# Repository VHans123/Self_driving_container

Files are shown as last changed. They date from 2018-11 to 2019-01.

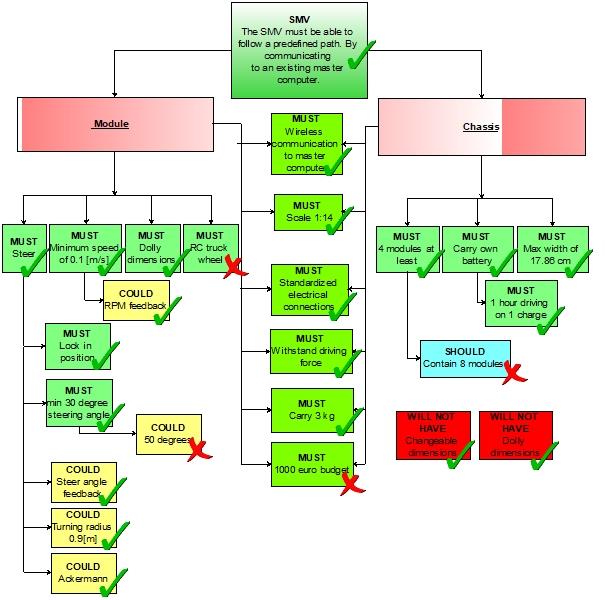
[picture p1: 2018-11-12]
Dallas/docs/Pictures/Check list requirements.jpg

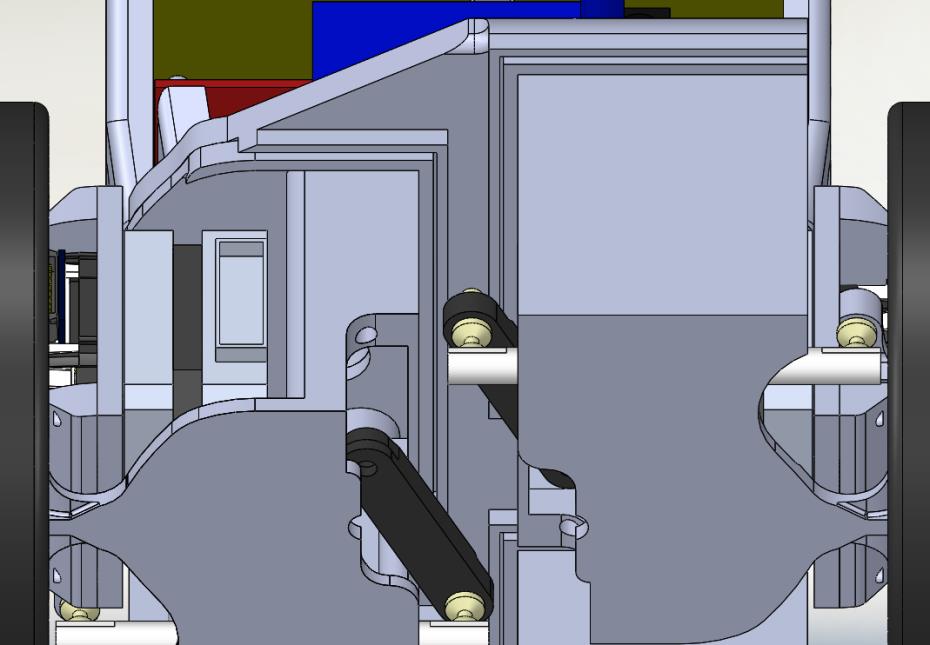
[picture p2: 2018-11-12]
Dallas/docs/Pictures/Chassis improvements 2.jpg

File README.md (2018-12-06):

# Self driving container

This is the repository of the self driving container chassis called Dolly.

It is split up in three main parts.

1 The first one is called Drawings. In this part you can find all the SolidWorks drawings of the chassis.

2 The second one is called Electronics. In this part you can find the Schematic design and PCB design of the PCB. These files are made in Multisim and Ultiboard.

3 The third one is called Software. In this part you can find all the Matlab and Simulink files. These files are used to receive data from the XBee. Also these files contain the software for controlling the wheel speed and angle.

The steering angle and speed of the Dolly is given by the Jetson. This Jetson uses a vision system. Because the vision system and the Dolly are two different parts, each one has it's one GitHub repositoy. Below you can find a link to the repository of the Jetson.

https://github.com/jostyijzer/ArUco-Detection

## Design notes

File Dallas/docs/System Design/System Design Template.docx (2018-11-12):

# System Design Template

Smart Quarter Vehicle

Status: Draft

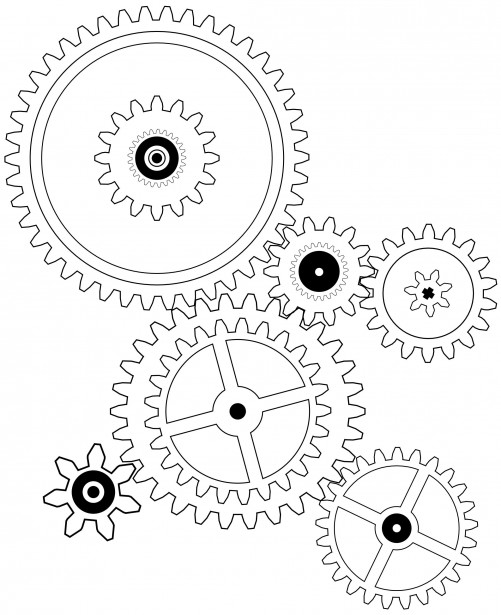
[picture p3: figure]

Name | Student nr
William Marcelissen | 507428
Chris van der Spek | 561633
Gerran Jansma | 521675
Teun van den Burg | 530770

# 1 Intro

During the project a Smart Modular Vehicle (SMV) will be designed, developed and built.

The Smart Modular Vehicle consists of a chassis and multiple identical and interchangeable steering and driving modules. The chassis and wheel dimensions will be scaled 1:14 with respect to a real truck. This SMV will be able to follow a predefined path by communicating with a master computer which has an overview of the predefined path via a camera hanging or hoovering above the path.

The SMV will be designed, developed and built for HAN Automotive Research. The SMV will provide them a modular platform which can simulate multiple truck chassis outlay. HAN AR can use this SMV for future and ongoing projects like the “Drone assisted truck navigation project”.

This system design document will first provide a general overview of the system and the goals of the project. It also contains a more detailed architecture and design of the system and all of its subsystems. These, more detailed, designs will both discuss hardware and software. The document will conclude with the design and architecture of the interface which will allow communication between the different subsystems. In this document the system will be visualised in diagrams to give the reader a better understanding of how all subsystems are connected.

# 2 General Overview and Design

## 2.1 General Overview

The system exists of the platform and at least four modules. The microcontroller of the system is placed on the platform and controls the steering, accelerating and braking of the four modules. The microcontroller communicates with the master computer which sends a signal that contains the predefined path.

## 2.2 System Context

Figure 1 Contextual Diagram

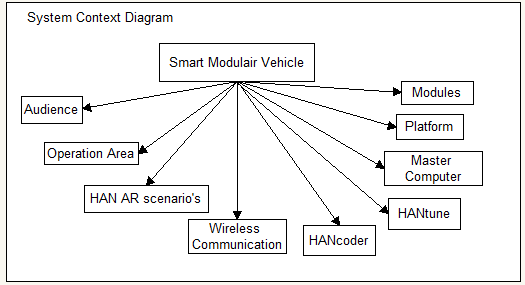
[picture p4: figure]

## 2.3 Use Cases

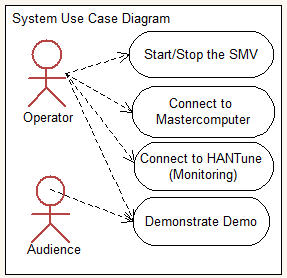
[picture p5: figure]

Figure 2 Use Case Diagram

### 2.3.1 System Components

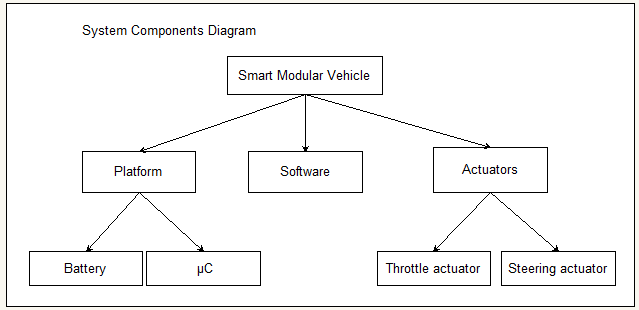
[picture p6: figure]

Figure 3 Component Diagram

## 2.4 Assumptions

- For creating and sending the predefined path to the SMV, the existing software developed by previous students will be used.
- The main software used for programming and debugging will be Matlab, Simulink, HANCoder and HANTune
- The end user can expect a Smart Modular Vehicle that is capable of driving the predefined path.
- The Smart modular Vehicle exist at least out of 4 modules (2 driving and 2 steering) but a different setup with more modules is possible.

## 2.5 Constraints

- The algorithms of the previous project group has to be investigated before changing and implanting is possible.
- Before the algorithms can be implemented, the platform with 4 modulus must be in prototype phase.
- Because the SMV is a prototype and there is a limited time frame, the end-user environment is not a high priority.

## 2.6 Risks

Because the project takes only roughly 3 months. The main focus will be the electrical and programming part of the system. Therefor the design of the SMV will be simple but sturdy, so no fancy boltless plug and play system for the modules will be developed. In this way there is more time that will be spent on programming and improving the system. What is more in the scope of this project.

# 3 Design Considerations

## 3.1 Problem Statement

The current vehicles are limited in their specifications and dimensions. Fixed truck setups and imprecise steering & driving makes these RC trucks undesired to work with.

As stated above, the current RC trucks are not precise enough in steering and driving. This concludes in a lot of steering actions that can be avoided with a better system. Also is HAN-AR limited in setup options, because of the fact that the truck setups are depending on the purchased vehicles.

## 3.2 Goals

The goal is to create a platform which makes use of wheel modules. This platform must drive a path that is predefined by the master computer.

- Within this main goal, a sub-goal is to create modular wheel units which receives input from the master PC.
- Another goal is to create a chassis that can accommodate at least 4 modules. The chassis needs standardised connections to connect with the modules.
- Also the modules will include (HANcoder) software to work properly.

# 4 System Architecture and Design

This chapter describes the different system aspects that could be used for the SMV. First thing that will be described is a logic view of the different system aspects that are going to be used on the SMV. The hardware architecture of the SMV will be described in different diagrams, after the logic view. The next step is also about architecture but then about the software that needs to be made. The last subject in this chapter is the internal communication of the SMV. All of this will be shown in diagrams and an explanation of the diagrams will be given.

## 4.1 Logical View

A logic view of a product is what it can do after it is turned on and off. The logical view of the SMV is presented here below.

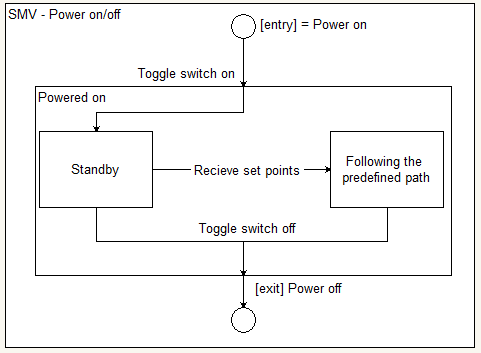
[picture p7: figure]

Figure 4 Logical view

## 4.2 Hardware Architecture

The hardware Architecture will be divide by the chassis and the module. The diagrams of the hardware architecture are shown below.

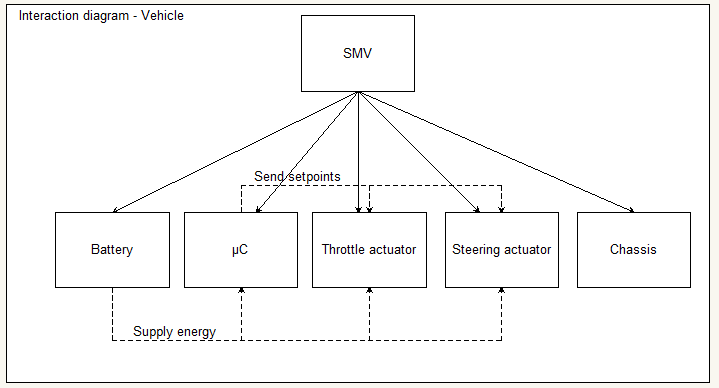
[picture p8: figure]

Figure 5 Interaction diagram of the vehicle

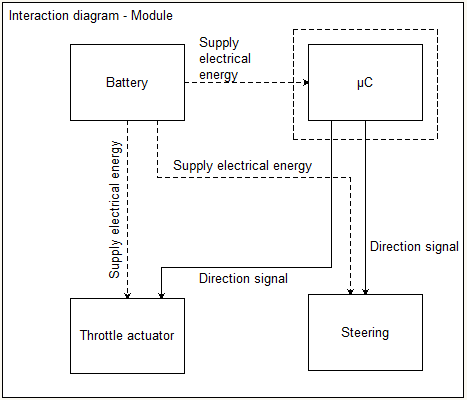
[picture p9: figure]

Figure 6 Interaction diagram of the module

## 4.3 Software Architecture

There needs to be a wireless connection between the master computer and the microcontroller. The microcontroller receives steering and throttle setpoints from the master computer. These setpoints have to be converted to a signal for the throttle and steering actuators of each individual module. Converting a single steering setpoint to multiple independent steering angles according to Ackermann is also done by the microcontroller.

## 4.4 Internal communication Architecture

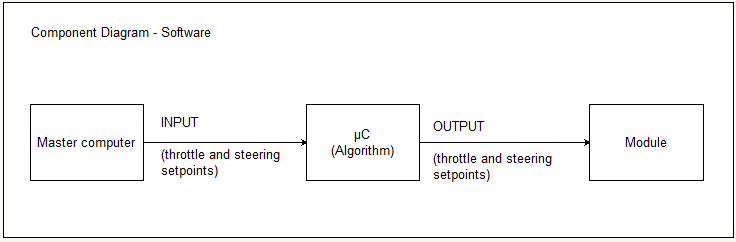
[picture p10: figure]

The communication of the SMV will be wireless from master computer to mainboard. The diagram of the wireless communication is shown in figure 7.

Figure 7 Wireless Interaction Diagram

# 5 System Detailed Design

## 5.1 Hardware Detailed Design

The SMV will contain both purchased components as components designed and built by the project group. To have a good overview of the hardware designed some components will be elaborated more detailed.

### 5.1.1 Chassis

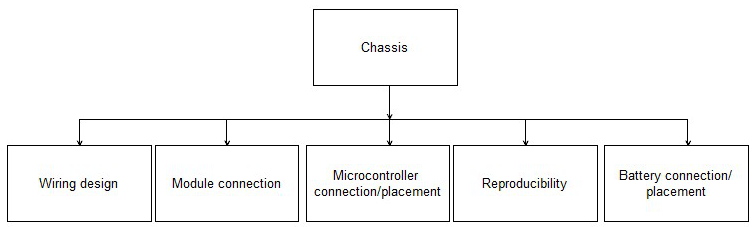
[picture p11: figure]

Figure 8 Chassis functions

The chassis is a large hardware component of the system. This component will carry all other subsystems, therefore it is important to have a more detailed look at the chassis.

Module connection

In the set of requirements is stated that de chassis must be able to carry at least four modules. These modules must be interchangeable. Therefore the connection between chassis and module must be modular. Another requirement states that the connection must be able to withstand the driving forces caused by driving the predefined path.

Mainboard connection/placement

The mainboard will be controlling all the modules and receive and process the signals coming from the master computer. The placement of this mainboard will be crucial for the design of the wiring.

Reproducibility

Because HAN AR is planning on using the SMV in different future projects, it is important for them to make more SMV’s. Therefore the design of the chassis should be accessible and adjustable to simulate a different vehicle. Also the production of the chassis should be easy to repeat.

Battery connection/placement

Being a heavy component the placement and connection of the battery is important for the design of the chassis.

### 5.1.2 Module

The modules are the most complex hardware components to be designed and built. A lot of functionalities of the SMV are dependent on the module design and development. Because of its importance the module design will be further specified.

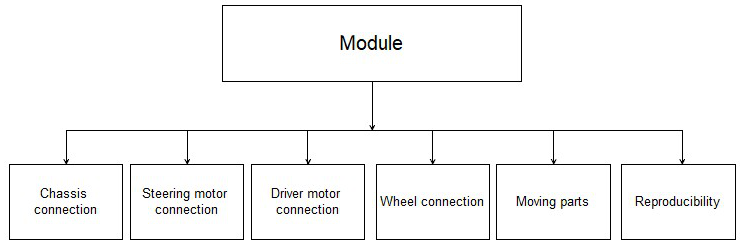
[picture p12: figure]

Chassis connection
This connection must be able to withstand the driving forces while driving the predefined path. See 5.1.1 Module connection.

Figure 9 Module functions

Steering motor connection

The steering motor will be connected to the module and the rest of the drivetrain. The connection to the module has to be rigid to set and hold a precise steering angle.

Driver motor connection

The driver motor needs a rigid connection to be able to deliver the driving force.

Wheel connection

HAN AR requires the use of existing 1:14 RC truck wheels.

Moving parts

Because of the steering capability of the modules there will be moving parts inside the module. This puts extra pressure on the tolerances of the hardware. While designing the modules this is an important fact to keep in mind.

Reproducibility

The module must be easy to reproduce to extend the SMV in future projects. This means accessible design and easy production methods.

## 5.2 Software Detailed Design

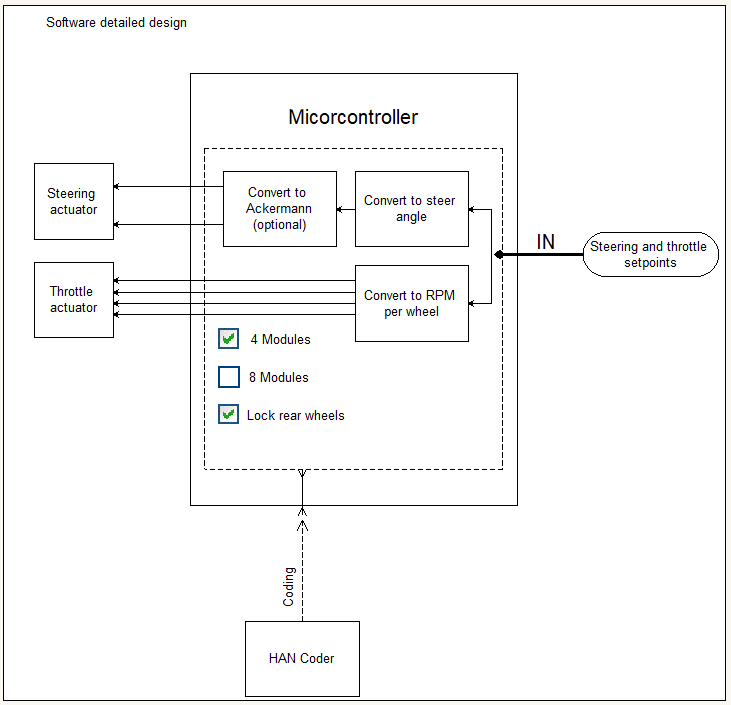
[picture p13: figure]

Figure 10 Software detailed design

The SMV will be communicating with the existing master computer, this computer will send out a signal to the SMV containing PWM values. The software programmed in de microcontroller will translate this to driving and steering the vehicle.

HAN Coder

The programming will be programmed using the model based HAN Coder software. Simulink blocks represent different functionalities. By placing these blocks a logical block diagram can be created. The C code will automatically be created by HAN Coder and can be flashed to the microcontroller.

Converting signals

The mainboard will receive its input from the master computer. The microcontroller has to convert this signal into an actual driving signal to the driver and steering motors. The driving signal the microcontroller has to transmit depends on the type of motors that will be used. The SMV might also get Ackermann steering behaviour, this will result in extra calculations of the microcontroller and different steering angles for each wheel.

Set up

HAN AR wants to use the SMV with a varying amount of modules connected. With the 4 wheel setup it should also be possible to lock the rear wheel which will prevent them from steering. This way a two wheel steering truck can be simulated. When changing the set up the driving signal also has to change. Therefore it is important that the set up changes in the software are straightforward and easy to make.

# 6 External Interfaces

Looking at the external interfaces used within this project, the main external interface is the Master computer. This project works with a predefined path that the Master computer sends in PWM signals to the SMV. The path can be defined in the master computer, or the path can be defined by the drone. Either way the master computer has coordinates of the path and sends it to the SMV.

## 6.1 Interface Architecture

Referring to the SCD, the master computer is a part of the whole system. The Master computer sends the PWM signals to the chassis. The Master computer receives the X, Y and angle of the vehicle via the drone. The logarithm calculates the PWM values to get the desired position of the vehicle.

Figure 11 System Context Diagram

## 6.2 Interface Detailed Design

Looking at the external interfaces, the master computer is the only and most important external interface.

Figure 12 Interaction diagram

Data Direction (Systems viewpoint) | What is interacted? | Details
Send | XCP messages over Zigbee | 4 bytes: Start byte, Steering byte with PWM value, throttle byte with PWM value, stop byte

It is possible that the Drone can send the predefined path to the master computer, in that case the Master computer receives the following data:

Data Direction (Systems viewpoint) | What is interacted? | Details
receive | XCP messages over Zigbee | 4 bytes: Start byte, Byte Marker 1 (X, Y, angle marker), Byte Marker 2(X, Y, angle marker), stop byte

# Appendix A – References

Diagrams:

Pictures:

# Appendix B – Diagram Conventions

These relations are a suggestion on how to use the diagrams. Feel free to add new features to your diagrams. However, if new features need to be added, please look at existing conventions in order to avoid confusion. At HAN-AR some knowledge and experience is present regarding formal modelling languages.

Component Diagram:

| Component (Also used in Interaction Diagrams)
| Component / Subcomponent relation (Also called: Parent/Child, or Super/Sub component)

Interaction Diagram:

| Component (from component diagram)
| Item flow (Anything that flows, e.g. Data, Energy, Fluid, Air)

State Machine Diagram:

| Entry point
| State
| Exit point
| State transition
| Guard, entry or exit criterium

Use Case Diagram:

| (Usually) Human interacting entity. Interaction may be both ways. Usually entails e.g. Operator, End-User, Maintenance staff, Audience, etc.
| A use case. Could also have descendants in order to group use cases.
| Interaction relation
| Descending relation

Document type System Design Template, Smart Quarter Vehicle Author/Project group Project Group SMV Project: Smart Quarter Vehicle Date 13- Oct-17 Document No 2 Issue 0.1 Status Draft Page No 5 of 18

HAN-AR 13 October 2017

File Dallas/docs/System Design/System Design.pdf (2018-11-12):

HAN-AR
13 October 2017

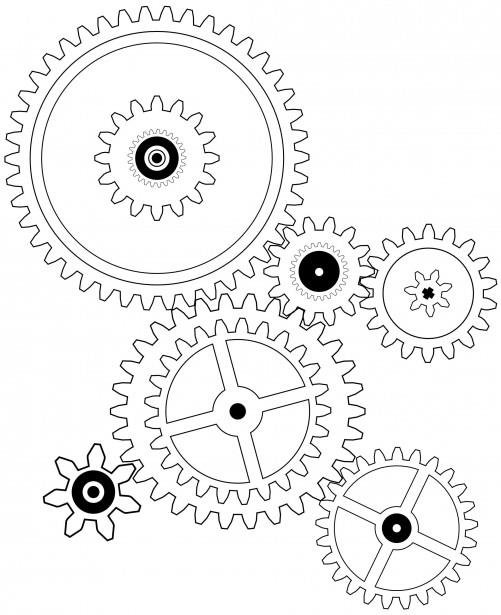
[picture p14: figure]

| Document type System Design Template, Smart Quarter Vehicle
Author/Project group Project Group SMV | Project: Smart Quarter Vehicle | Date 13- Oct-17
Document No | Issue 0.1 | Status Draft | Page No

# System Design Template

## Smart Quarter Vehicle

Status: Draft

Name | Student nr
William Marcelissen | 507428
Chris van der Spek | 561633
Gerran Jansma | 521675
Teun van den Burg | 530770

Document type

## Table of Contents

Document type

## 1 Intro

During the project a Smart Modular Vehicle (SMV) will be designed, developed and built.
The Smart Modular Vehicle consists of a chassis and multiple identical and interchangeable steering and driving modules. The chassis and wheel dimensions will be scaled 1:14 with respect to a real truck. This SMV will be able to follow a predefined path by communicating with a master computer which has an overview of the predefined path via a camera hanging or hoovering above the path.

The SMV will be designed, developed and built for HAN Automotive Research. The SMV will provide them a modular platform which can simulate multiple truck chassis outlay. HAN AR can use this SMV for future and ongoing projects like the “Drone assisted truck navigation project”.

This system design document will first provide a general overview of the system and the goals of the project. It also contains a more detailed architecture and design of the system and all of its subsystems. These, more detailed, designs will both discuss hardware and software. The document will conclude with the design and architecture of the interface which will allow communication between the different subsystems. In this document the system will be visualised in diagrams to give the reader a better understanding of how all subsystems are connected.

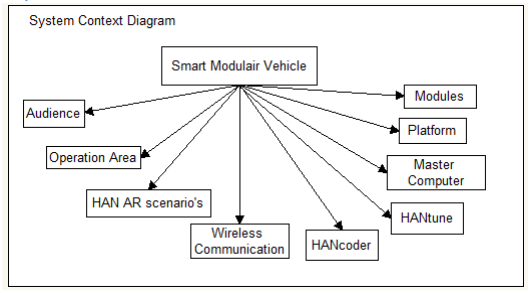
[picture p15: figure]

Document type

## 2 General Overview and Design

### 2.1 General Overview

The system exists of the platform and at least four modules. The microcontroller of the system is placed on the platform and controls the steering, accelerating and braking of the four modules. The microcontroller communicates with the master computer which sends a signal that contains the predefined path.

### 2.2 System Context

### 2.3 Use Cases

Figure 2 Use Case Diagram

Figure 1 Contextual Diagram


Document type

2.3.1 System Components

### 2.4 Assumptions

- For creating and sending the predefined path to the SMV, the existing software developed by previous students will be used.
- The main software used for programming and debugging will be Matlab, Simulink, HANCoder and HANTune
- The end user can expect a Smart Modular Vehicle that is capable of driving the predefined path.
- The Smart modular Vehicle exist at least out of 4 modules (2 driving and 2 steering) but a different setup with more modules is possible.

### 2.5 Constraints

- The algorithms of the previous project group has to be investigated before changing and implanting is possible.
- Before the algorithms can be implemented, the platform with 4 modulus must be in prototype phase.
- Because the SMV is a prototype and there is a limited time frame, the end-user environment is not a high priority.

Figure 3 Component Diagram

Document type

### 2.6 Risks

Because the project takes only roughly 3 months. The main focus will be the electrical and programming part of the system. Therefor the design of the SMV will be simple but sturdy, so no fancy boltless plug and play system for the modules will be developed. In this way there is more time that will be spent on programming and improving the system. What is more in the scope of this project.

## 3 Design Considerations

### 3.1 Problem Statement

The current vehicles are limited in their specifications and dimensions. Fixed truck setups and imprecise steering & driving makes these RC trucks undesired to work with.

As stated above, the current RC trucks are not precise enough in steering and driving. This concludes in a lot of steering actions that can be avoided with a better system. Also is HAN-AR limited in setup options, because of the fact that the truck setups are depending on the purchased vehicles.

### 3.2 Goals

The goal is to create a platform which makes use of wheel modules. This platform must drive a path that is predefined by the master computer.

- Within this main goal, a sub-goal is to create modular wheel units which receives input from the master PC.
- Another goal is to create a chassis that can accommodate at least 4 modules. The chassis needs standardised connections to connect with the modules.
- Also the modules will include (HANcoder) software to work properly.


Document type

## 4 System Architecture and Design

This chapter describes the different system aspects that could be used for the SMV. First thing that will be described is a logic view of the different system aspects that are going to be used on the SMV. The hardware architecture of the SMV will be described in different diagrams, after the logic view. The next step is also about architecture but then about the software that needs to be made. The last subject in this chapter is the internal communication of the SMV. All of this will be shown in diagrams and an explanation of the diagrams will be given.

### 4.1 Logical View

A logic view of a product is what it can do after it is turned on and off. The logical view of the SMV is presented here below.

Figure 4 Logical view

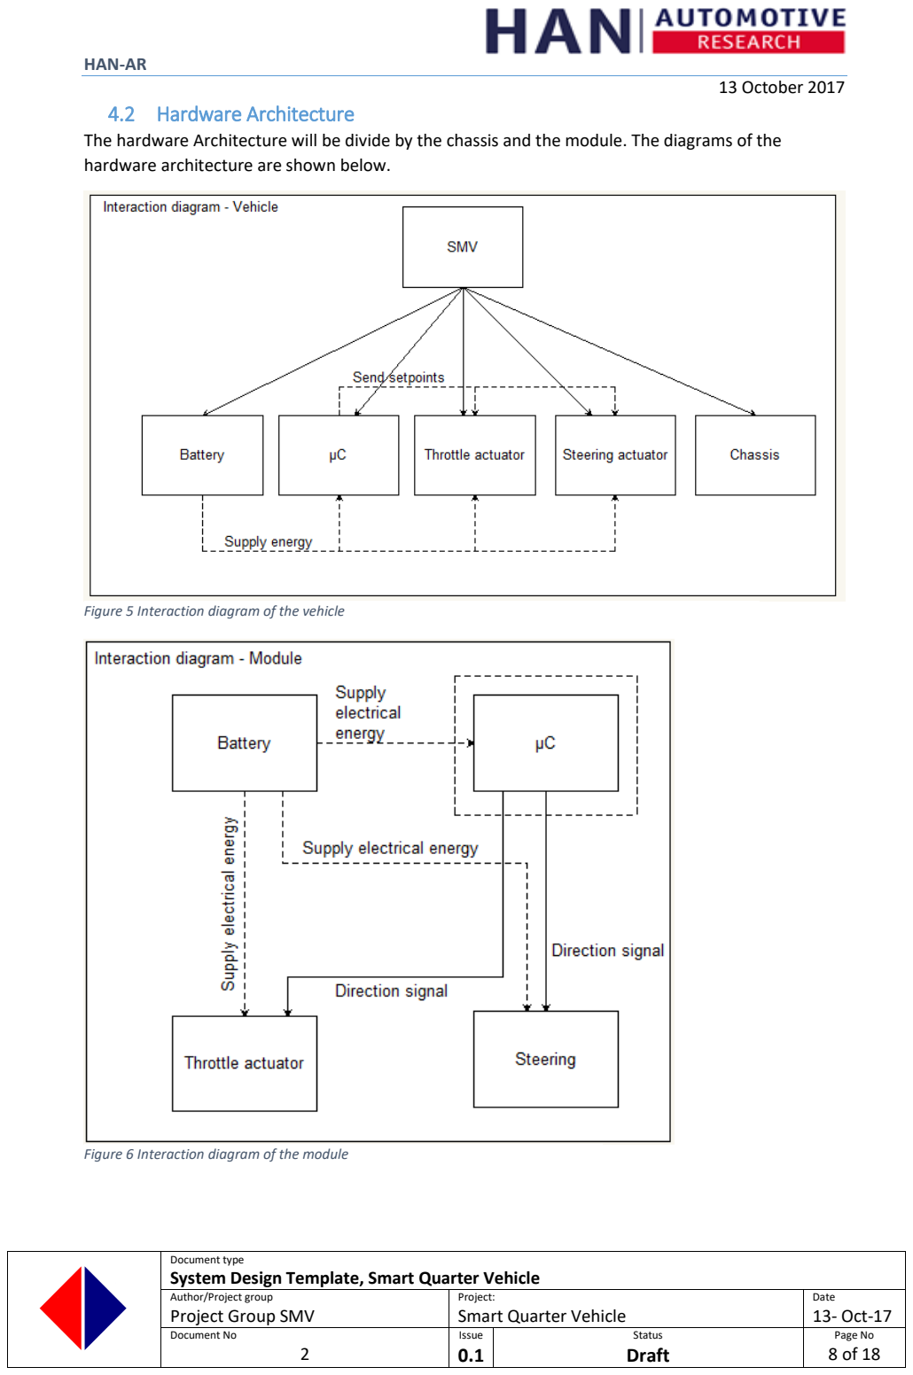
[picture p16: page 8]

Document type

### 4.2 Hardware Architecture

The hardware Architecture will be divide by the chassis and the module. The diagrams of the hardware architecture are shown below.

Figure 5 Interaction diagram of the vehicle

Figure 6 Interaction diagram of the module

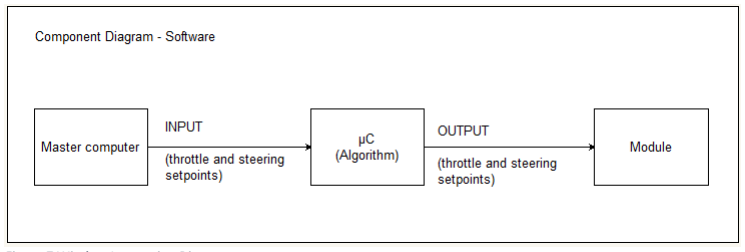
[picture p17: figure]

Document type

### 4.3 Software Architecture

There needs to be a wireless connection between the master computer and the microcontroller. The microcontroller receives steering and throttle setpoints from the master computer. These setpoints have to be converted to a signal for the throttle and steering actuators of each individual module. Converting a single steering setpoint to multiple independent steering angles according to Ackermann is also done by the microcontroller.

### 4.4 Internal communication Architecture

The communication of the SMV will be wireless from master computer to mainboard. The diagram of the wireless communication is shown in figure 7.

Figure 7 Wireless Interaction Diagram

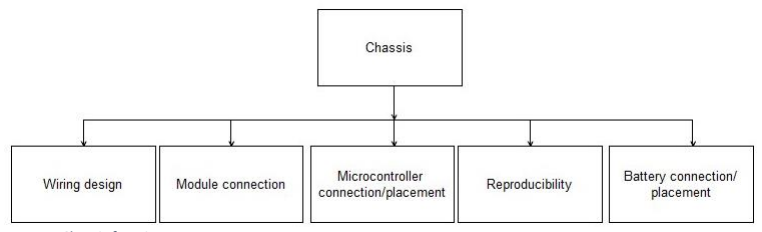
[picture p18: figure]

Document type

## 5 System Detailed Design

### 5.1 Hardware Detailed Design

The SMV will contain both purchased components as components designed and built by the project group. To have a good overview of the hardware designed some components will be elaborated more detailed.

5.1.1 Chassis

The chassis is a large hardware component of the system. This component will carry all other subsystems, therefore it is important to have a more detailed look at the chassis.

Module connection
In the set of requirements is stated that de chassis must be able to carry at least four modules. These modules must be interchangeable. Therefore the connection between chassis and module must be modular. Another requirement states that the connection must be able to withstand the driving forces caused by driving the predefined path.

Mainboard connection/placement
The mainboard will be controlling all the modules and receive and process the signals coming from the master computer. The placement of this mainboard will be crucial for the design of the wiring.

Reproducibility
Because HAN AR is planning on using the SMV in different future projects, it is important for them to make more SMV’s. Therefore the design of the chassis should be accessible and adjustable to simulate a different vehicle. Also the production of the chassis should be easy to repeat.

Battery connection/placement
Being a heavy component the placement and connection of the battery is important for the design of the chassis.

Figure 8 Chassis functions

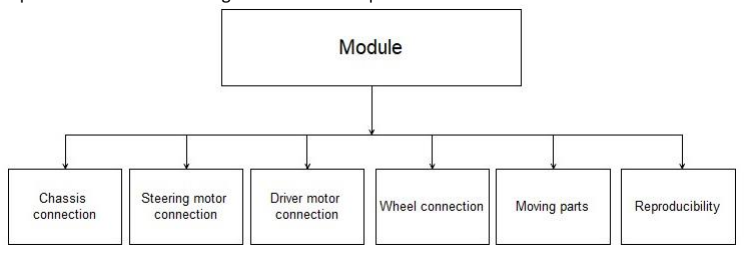
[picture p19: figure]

Document type

5.1.2 Module
The modules are the most complex hardware components to be designed and built. A lot of functionalities of the SMV are dependent on the module design and development. Because of its importance the module design will be further specified.

Chassis connection
This connection must be able to withstand the driving forces while driving the predefined path. See 5.1.1 Module connection.

Steering motor connection
The steering motor will be connected to the module and the rest of the drivetrain. The connection to the module has to be rigid to set and hold a precise steering angle.

Driver motor connection
The driver motor needs a rigid connection to be able to deliver the driving force.

Wheel connection
HAN AR requires the use of existing 1:14 RC truck wheels.

Moving parts
Because of the steering capability of the modules there will be moving parts inside the module. This puts extra pressure on the tolerances of the hardware. While designing the modules this is an important fact to keep in mind.

Reproducibility
The module must be easy to reproduce to extend the SMV in future projects. This means accessible design and easy production methods.

Figure 9 Module functions

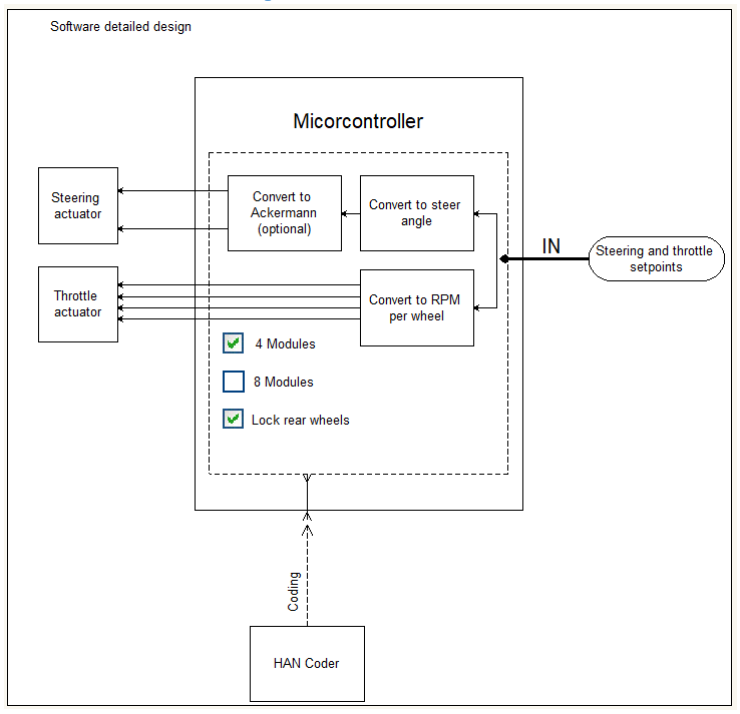
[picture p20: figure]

Document type

### 5.2 Software Detailed Design

The SMV will be communicating with the existing master computer, this computer will send out a signal to the SMV containing PWM values. The software programmed in de microcontroller will translate this to driving and steering the vehicle.
HAN Coder
The programming will be programmed using the model based HAN Coder software. Simulink blocks represent different functionalities. By placing these blocks a logical block diagram can be created. The C code will automatically be created by HAN Coder and can be flashed to the microcontroller.

Converting signals
The mainboard will receive its input from the master computer. The microcontroller has to convert this signal into an actual driving signal to the driver and steering motors. The driving signal the microcontroller has to transmit depends on the type of motors that will be used. The SMV might also get Ackermann steering behaviour, this will result in extra calculations of the microcontroller and different steering angles for each wheel.

Figure 10 Software detailed design

Document type

Set up
HAN AR wants to use the SMV with a varying amount of modules connected. With the 4 wheel setup it should also be possible to lock the rear wheel which will prevent them from steering. This way a two wheel steering truck can be simulated. When changing the set up the driving signal also has to change. Therefore it is important that the set up changes in the software are straightforward and easy to make.

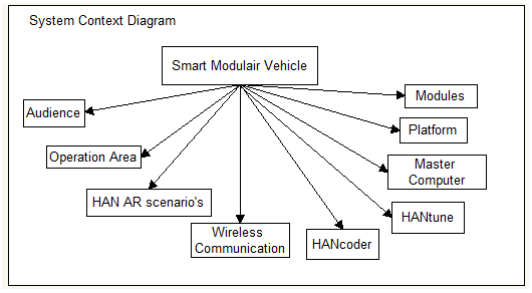
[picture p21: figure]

Document type

## 6 External Interfaces

Looking at the external interfaces used within this project, the main external interface is the Master computer. This project works with a predefined path that the Master computer sends in PWM signals to the SMV. The path can be defined in the master computer, or the path can be defined by the drone. Either way the master computer has coordinates of the path and sends it to the SMV.

### 6.1 Interface Architecture

Referring to the SCD, the master computer is a part of the whole system. The Master computer sends the PWM signals to the chassis. The Master computer receives the X, Y and angle of the vehicle via the drone. The logarithm calculates the PWM values to get the desired position of the vehicle.

Figure 11 System Context Diagram

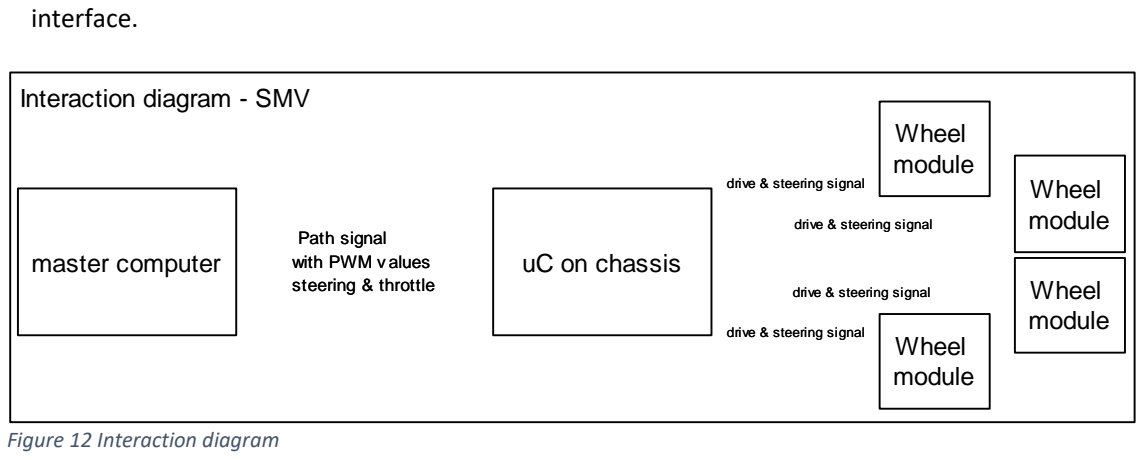
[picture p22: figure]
interface.; Interaction diagram - SMV; master computer; uC on chassis; Wheel module; Path signal with PWM v alues steering & throttle; drive & steering signal; Figure 12 Interaction diagram

Document type

### 6.2 Interface Detailed Design

Looking at the external interfaces, the master computer is the only and most important external

Data Direction (Systems viewpoint) | What is interacted? | Details
Send | XCP messages over Zigbee | 4 bytes: Start byte, Steering byte with PWM value, throttle byte with PWM value, stop byte

It is possible that the Drone can send the predefined path to the master computer, in that case the Master computer receives the following data:

Data Direction (Systems viewpoint) | What is interacted? | Details
receive | XCP messages over Zigbee | 4 bytes: Start byte, Byte Marker 1 (X, Y, angle marker), Byte Marker 2(X, Y, angle marker), stop byte

Document type

## Appendix A – References

Diagrams:

Figure 1: Contextual Diagram | Fout! Bladwijzer niet gedefinieerd.
Figure 2: Use Case Diagram | Fout! Bladwijzer niet gedefinieerd.
Figure 3: Component Hierarchy | Fout! Bladwijzer niet gedefinieerd.
Figure 4: State Machine: Balancing the Suitcase | Fout! Bladwijzer niet gedefinieerd.
Figure 5: State Machine: Connection to HANtune | Fout! Bladwijzer niet gedefinieerd.
Figure 6: Interaction Diagram - Power Supply | Fout! Bladwijzer niet gedefinieerd.
Figure 7: Interaction Diagram - HANtune Connection via WiFi .......Fout! Bladwijzer niet gedefinieerd.

Pictures:

Picture 1: Balancing Suitcase Demo | Fout! Bladwijzer niet gedefinieerd.

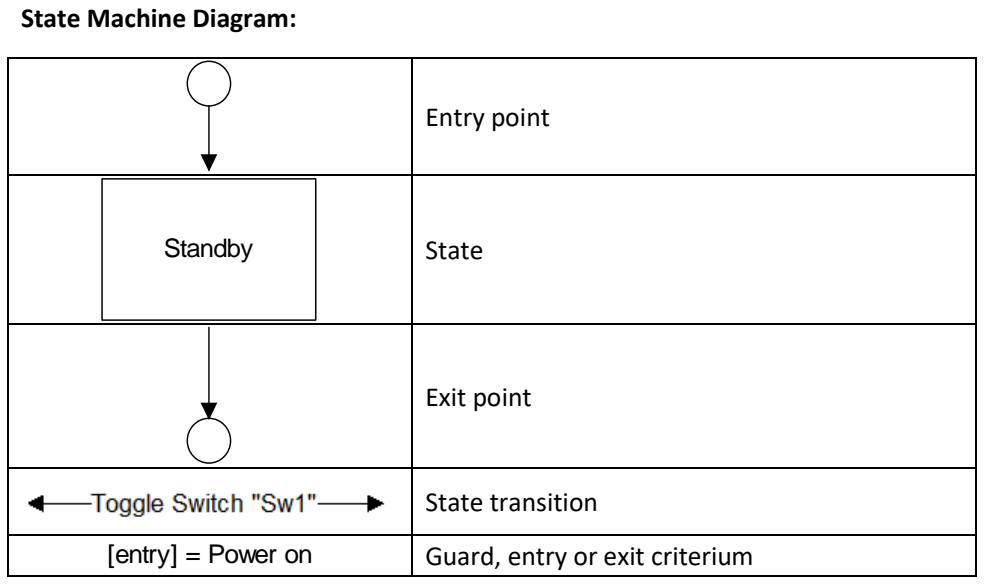
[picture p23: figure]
State Machine Diagram:; Entry point; State; Exit point; State transition; Guard, entry or exit criterium

Document type

## Appendix B – Diagram Conventions

These relations are a suggestion on how to use the diagrams. Feel free to add new features to your diagrams. However, if new features need to be added, please look at existing conventions in order to avoid confusion. At HAN-AR some knowledge and experience is present regarding formal modelling languages.

Component Diagram:

Component (Also used in Interaction Diagrams)

Component / Subcomponent relation (Also called: Parent/Child, or Super/Sub component)

Interaction Diagram:

Component (from component diagram)

Item flow (Anything that flows, e.g. Data, Energy, Fluid, Air)

# Balancing Suitcase Demo DC-Motor Standby [entry] = Power on

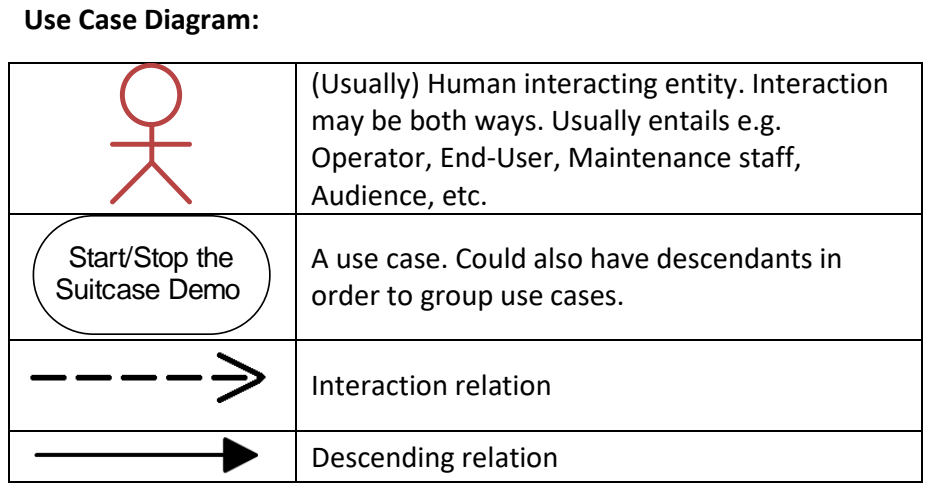
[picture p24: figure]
Use Case Diagram:; Interaction relation; Descending relation

Document type

| (Usually) Human interacting entity. Interaction may be both ways. Usually entails e.g. Operator, End-User, Maintenance staff, Audience, etc.
Start/Stop the Suitcase Demo | A use case. Could also have descendants in order to group use cases.

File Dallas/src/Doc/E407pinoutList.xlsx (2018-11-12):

HANcoder E407 Pinout list
You can use this list to check whether you will have sufficient I/O for your project. Every pin can have only 1 function.
The pin naming is the name of the pin on the connector, i.e. PD7 is pin 7 on connector PD
Pin | AI | AO | CAN | DI | DO | FL | PWM | SPI | SPI CS | QEG | TIG | TIM IRQ | UART | Eth | USB |  | AI = Analog Input
A0 | x |  |  | x | x |  |  |  | x |  |  |  |  |  |  |  | AO = Analog Output
A1 | x |  |  | x | x |  | x |  | x |  |  |  |  |  |  |  | DI = Digital Input
A2 | x |  |  | x | x |  | x |  | x |  |  |  |  |  |  |  | DO = Digital Output
A3 | x |  |  | x | x |  | x |  | x |  |  |  |  |  |  |  | FL = File Logger
A4 | x |  |  | x | x |  | x |  | x |  |  |  |  |  |  |  | PWM = Pulse Width Modulation
A5 | x |  |  | x | x |  |  |  | x |  |  |  |  |  |  |  | SPI = Data and clock lines of SPI
D0 |  |  |  | x | x |  |  |  | x |  |  |  | x |  |  |  | SPI CS = Chip Select/Slave Select
D1 |  |  | x | x | x |  |  |  | x |  |  |  | x |  |  |  | QEG = Quadrature Encoder Get
D2 |  |  |  | x | x |  |  |  | x |  |  |  |  |  |  |  | TIG = Timer Input Get
D3 |  |  |  | x | x |  |  |  | x |  |  |  |  |  |  |  | TIM IRQ = Timer Input IRQ + Compare Event IRQ + Get Last Event Counter + Schedule Compare Event
D4 |  |  |  | x | x |  | x |  | x |  | x | x |  |  |  |  | Eth = Ethernet
D5 |  |  |  | x | x |  | x |  | x |  | x | x
D6 |  |  |  | x | x |  |  |  | x |  |  |  |  |  |  |  |  | = Communication protocol pins for a connection to HANtune
D7 |  |  |  | x | x |  |  |  | x |  |  |  |  |  |  |  |  | = Unused pins
D8 |  |  |  | x | x |  |  |  | x
D9 |  |  |  | x | x |  |  |  | x
D10 |  | x |  | x | x |  |  |  | x
D11 |  |  | x | x | x |  | x | x | x | x | x | x
D12 |  |  |  | x | x |  | x | x | x | x | x | x
D13 |  | x |  | x | x |  | x | x | x |  | x | x
PD3 |  |  | x | x | x |  |  |  | x
PD4 |  |  | x | x | x |  |  |  | x
PD5 |  |  |  | x | x | x |  |  | x
PD6 |  |  |  | x | x |  |  |  | x
PD7 |  |  |  | x | x |  |  |  | x
PD8 |  |  |  | x | x |  |  |  | x |  |  |  | x
PD9 |  |  |  | x | x |  |  |  | x |  |  |  | x
PD10 |  |  |  | x | x |  |  |  | x
PD11 |  |  |  | x | x |  |  |  | x |  |  |  | x
PD12 |  |  |  | x | x |  |  |  | x |  |  |  | x
PD13 |  |  |  | x | x |  |  |  | x
PD14 |  |  |  | x | x |  |  |  | x
PD15 |  |  |  | x | x |  | x |  | x | x | x | x
PD16 |  |  |  | x | x |  | x |  | x | x | x | x
PD17 |  |  |  | x | x |  |  |  | x
PD18 |  |  |  | x | x |  |  |  | x
PE3 |  |  |  | x | x |  |  |  | x
PE4 |  |  |  | x | x |  |  |  | x
PE5/D2 |  |  |  | x | x |  |  |  | x
PE6 |  |  |  | x | x |  |  |  | x
PE7/D3 |  |  |  | x | x |  |  |  | x
PE8/D4 |  |  |  | x | x |  | x |  | x |  | x | x
PE9/D5 |  |  |  | x | x |  | x |  | x |  | x | x
PE10 |  |  |  | x | x |  |  |  | x
PE11 |  |  |  | x | x |  | x |  | x
PE12 |  |  |  | x | x |  | x |  | x | x | x | x
PE13 |  |  |  | x | x |  | x |  | x
PE14 |  |  |  | x | x |  | x |  | x | x | x | x
PE15 |  |  |  | x | x |  | x |  | x
PE16 |  |  |  | x | x |  | x |  | x |  | x | x
PE17 |  |  |  | x | x |  | x |  | x |  | x | x
PE18 |  |  |  | x | x |  |  |  | x
PF3 |  |  |  | x | x |  |  |  | x
PF4 |  |  |  | x | x |  |  |  | x
PF5 |  |  |  | x | x |  |  |  | x
PF6 | x |  |  | x | x |  |  |  | x
PF7 | x |  |  | x | x |  |  |  | x
PF8 | x |  |  | x | x |  |  |  | x
PF9/A1 | x |  |  | x | x |  | x |  | x |  | x | x
PF10/A2 | x |  |  | x | x |  | x |  | x |  | x | x
PF11/A3 | x |  |  | x | x |  | x |  | x |  | x | x
PF12/A4 | x |  |  | x | x |  | x |  | x |  | x | x
PF13/A5 | x |  |  | x | x |  |  |  | x
PF14 |  |  |  | x | x |  |  |  | x
PF15 |  |  |  | x | x |  |  |  | x
PF16 |  |  |  | x | x |  |  |  | x
PF17 |  |  |  | x | x |  |  |  | x
PF18 |  |  |  | x | x |  |  |  | x
PG3 |  |  |  | x | x |  |  |  | x
PG4 |  |  |  | x | x |  |  |  | x
PG5 |  |  |  | x | x |  |  |  | x
PG6 |  |  |  | x | x |  |  |  | x
PG7 |  |  |  | x | x |  |  |  | x
PG8 |  |  |  | x | x |  |  |  | x
PG9 |  |  |  | x | x |  |  |  | x
PG10/D6 |  |  |  | x | x |  |  |  | x
PG11/D7 |  |  |  | x | x |  |  |  | x
PG12/D8 |  |  |  | x | x |  |  |  | x
PG13 |  |  |  | x | x |  |  |  | x
PG14 |  |  |  | x | x |  |  |  | x |  |  |  |  | x
PG15 |  |  |  | x | x |  |  |  | x
PG16 |  |  |  | x | x |  |  |  | x |  |  |  |  | x
PG17 |  |  |  | x | x |  |  |  | x |  |  |  |  | x
PG18/D9 |  |  |  | x | x |  |  |  | x
UEXT3 |  |  |  |  |  |  | x |  |  | x | x | x | x
UEXT4 |  |  |  |  |  |  | x |  |  | x | x | x | x
UEXT5 |  |  |  |  |  |  |  |  |  |  |  |  |  |  |  | I2C1_SCL
UEXT6 |  |  |  |  |  |  |  |  |  |  |  |  |  |  |  | I2C1_SDA
UEXT7 | x |  |  |  |  |  |  | x
UEXT8 |  |  |  |  |  |  |  | x
UEXT9 |  |  |  |  |  |  |  | x
UEXT10 |  |  |  |  |  |  |  |  |  |  |  |  |  |  |  | UEXT_CS/StackOverflowDetected
WakeUp |  |  |  | x
LED |  |  |  |  | x
TIM1 |  |  |  |  |  |  | x |  |  |  | x | x
TIM2 |  |  |  |  |  |  | x |  |  |  | x | x
TIM3 |  |  |  |  |  |  | x |  |  |  | x | x
TIM4 |  |  |  |  |  |  | x |  |  |  | x | x
TIM8 |  |  |  |  |  |  | x |  |  |  | x | x
TIM9 |  |  |  |  |  |  | x |  |  |  | x | x
TIM10 |  |  |  |  |  |  | x |  |  |  | x | x
TIM11 |  |  |  |  |  |  | x |  |  |  | x | x
TIM13 |  |  |  |  |  |  | x |  |  |  | x | x
TIM14 |  |  |  |  |  |  | x |  |  |  | x | x

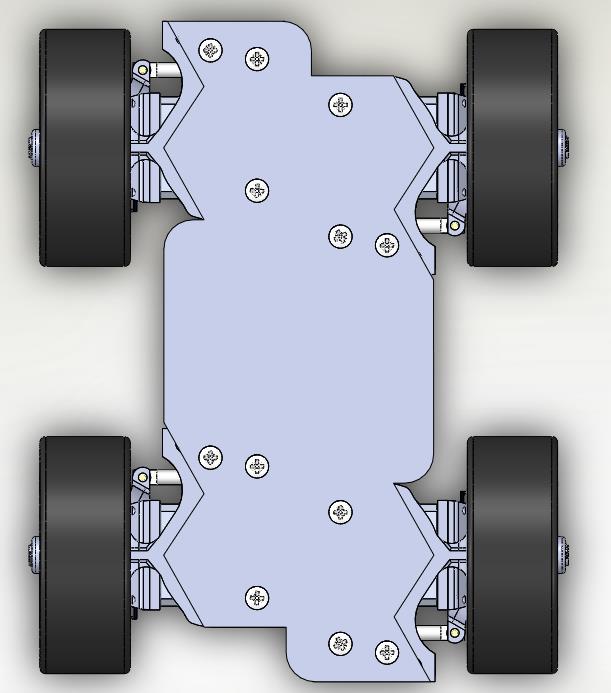
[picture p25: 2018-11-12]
Dallas/docs/Pictures/Chassis bottom view.jpg

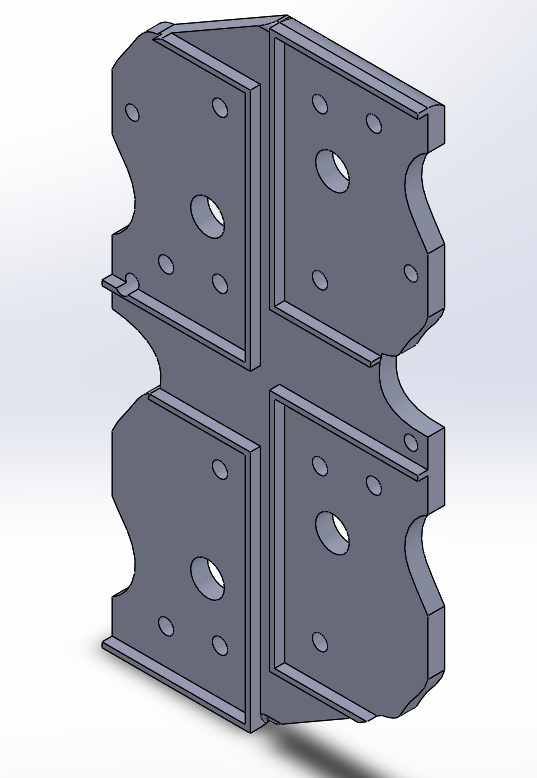
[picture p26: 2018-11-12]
Dallas/docs/Pictures/Chassis improvements.png

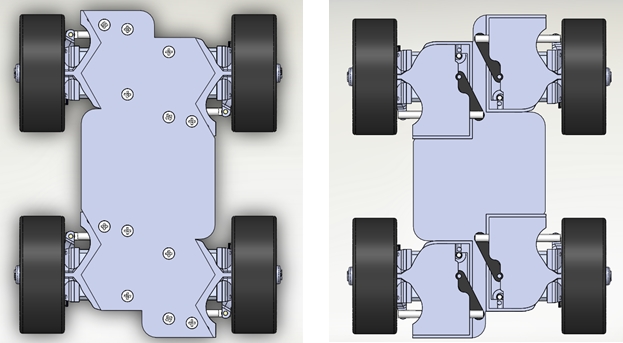
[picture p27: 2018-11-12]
Dallas/docs/Pictures/Chassis.jpg

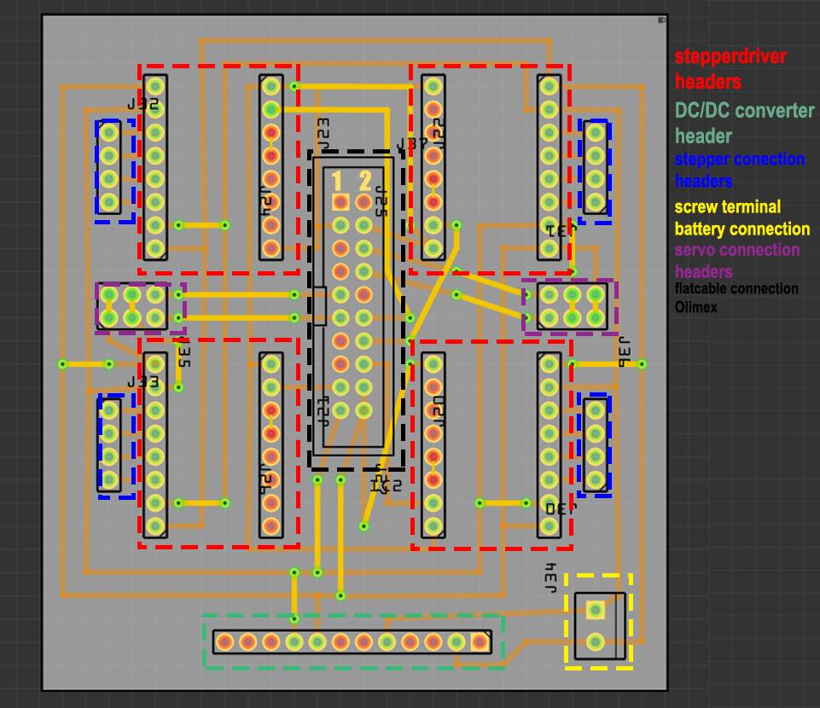
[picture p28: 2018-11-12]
Dallas/docs/Pictures/PCB design.jpg

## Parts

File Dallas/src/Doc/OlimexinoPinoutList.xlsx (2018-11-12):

HANcoder Olimexino Pinout list
You can use this list to check whether you will have sufficient I/O for your project. Every pin can have only 1 function.
The pin naming is the name of the pin on the connector
Pin | AI | CAN | DI | DO | FL | PWM | SPI | SPI CS | QEG | TIG | TIM IRQ | UART | USB |  | AI = Analog Input
A0 | x |  | x | x |  |  |  | x |  |  |  |  |  |  | DI = Digital Input
A1 | x |  | x | x |  |  |  | x |  |  |  |  |  |  | DO = Digital Output
A2 | x |  | x | x |  |  |  | x |  |  |  |  |  |  | FL = File Logger
A3 | x |  | x | x |  |  |  | x |  |  |  |  |  |  | PWM = Pulse Width Modulation
A4 | x |  | x | x |  |  |  | x |  |  |  |  |  |  | SPI = Data and clock lines of SPI
A5 | x |  | x | x |  |  |  | x |  |  |  |  |  |  | SPI CS = Chip Select/Slave Select
D0 | x |  | x | x |  | x |  | x |  | x | x | x |  |  | QEG = Quadrature Encoder Get
D1 | x |  | x | x |  |  |  | x |  | x | x | x |  |  | TIG = Timer Input Get
D2 | x |  | x | x |  | x |  | x | x | x | x |  |  |  | TIM IRQ = Timer Input IRQ + Compare Event IRQ + Get Last Event Counter + Schedule Compare Event
D3/LED2 | x |  | x | x |  | x |  | x | x | x | x
D4 |  |  | x | x |  |  |  | x |  |  |  |  |  |  |  | = Communication protocol pins for a connection to HANtune
D5 |  |  | x | x |  | x |  | x | x | x | x |  |  |  |  | = Unused pins
D6 |  |  | x | x |  | x |  | x | x | x | x
D7 |  |  | x | x |  | x |  | x | x | x | x | x
D8 |  |  | x | x |  | x |  | x |  | x | x | x
D9 |  |  | x | x |  | x |  | x | x | x | x
D10 | x |  | x | x |  |  |  | x
D11 | x |  | x | x |  |  | x | x
D12 | x |  | x | x |  |  | x | x
D13\LED1 | x |  | x | x |  |  | x | x
D14 |  | x |  |  |  | x |  |  |  | x | x
D24 |  | x |  |  |  | x |  |  |  | x | x
D25 |  |  | x | x | x |  |  | x
D26 |  |  |  |  |  |  |  |  |  |  |  |  |  | Pin high if stack overflow detected
D27
D28
D29 |  |  | x |  |  |  |  |  |  |  |  | x
D30 |  |  | x |  |  |  |  |  |  |  |  | x
D31 |  |  | x | x |  |  |  | x
D32 |  |  | x | x | x | x | x | x
D33 |  |  | x |  | x | x | x
D34 |  |  | x |  | x | x | x
D35 |  |  | x | x |  | x |  | x | x | x | x
D36 |  |  | x | x |  | x |  | x | x | x | x
D37 |  |  | x | x |  | x |  | x |  | x | x
BUT |  |  | x
TIM1 |  |  |  |  |  | x | ? |  | x | x |  | ?
TIM2 |  |  |  |  |  | x | ? |  | x | x |  | ?
TIM3 |  |  |  |  |  | x | ? |  | x | x |  | ?
TIM4 |  |  |  |  |  | x | ? |  | x | x |  | ?

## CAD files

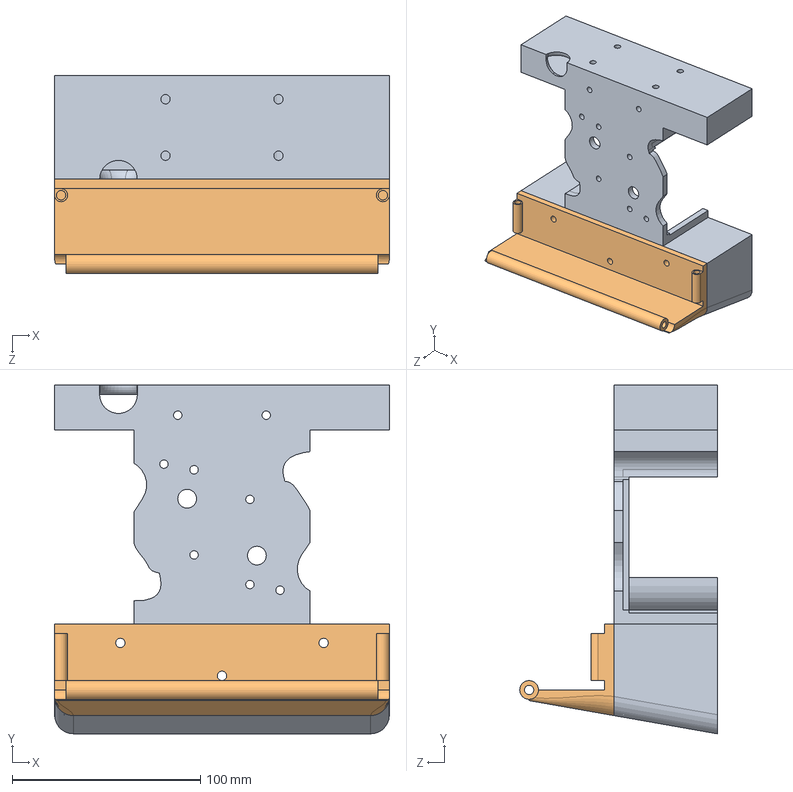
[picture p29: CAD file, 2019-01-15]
Backup_drawings/Self_driving_container-master/Drawings/Assem1.SLDASM
178.0 x 185.2 x 105.0 mm
Dolly chassis half 1
Foldable front base 2

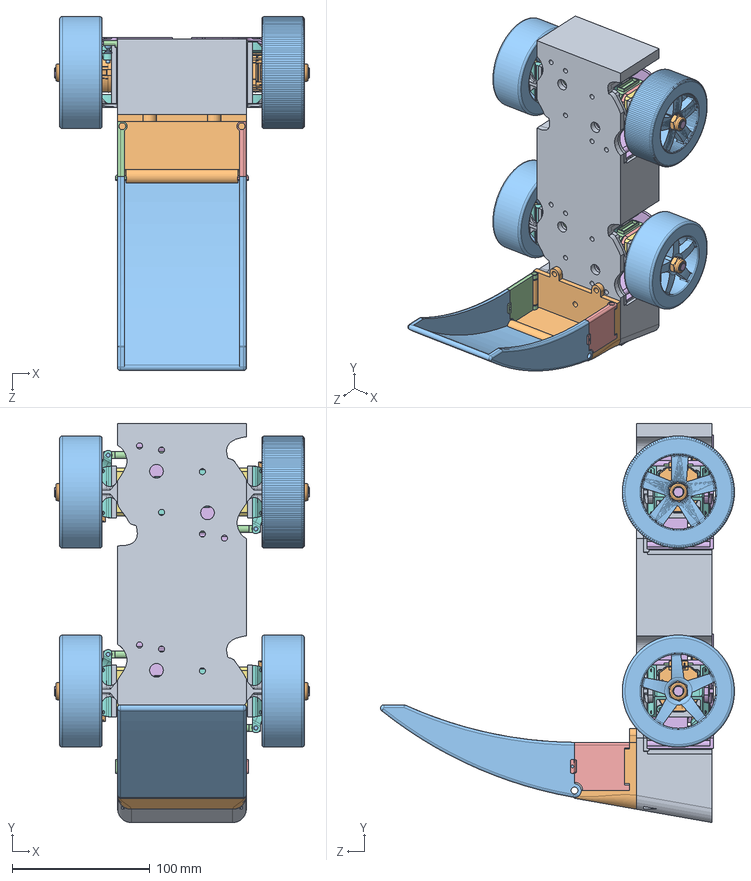
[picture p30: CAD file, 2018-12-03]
Backup_drawings/Self_driving_container-master/Drawings/Dolly_Assembly/Assembly dolly.SLDASM
185.4 x 290.0 x 257.2 mm
Dolly chassis test
Foldable front base
foldable front flap
Foldable front side flap
Foldable front side flap left
Housing x 4
Bearing 12x8 x 8
Spindle x 4
Spindle base x 4
Encoder x 4
nema14_base x 4
nema14_centro x 4
nema14_eje x 4
nema14_techo x 4
TowerPro-SG90-Body x 4
ServoFinalGear x 4
Control arm x 4
Ball x 8
Joint x 8
Steering rod x 4
Wheel adapter x 4
Wheel spacer x 4
M3x5 din 7984 x 32
Housing lid x 4
M8 nut x 4
Wheel x 4

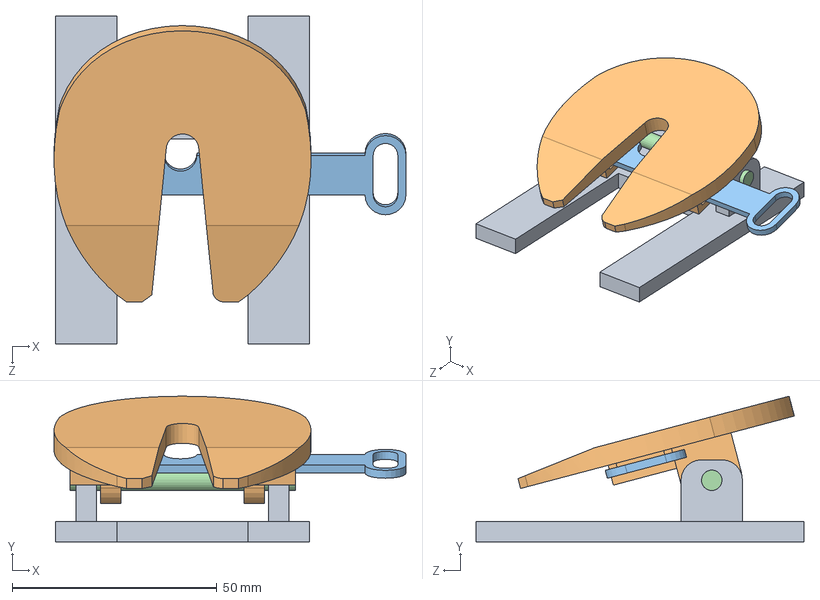
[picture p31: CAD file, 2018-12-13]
Backup_drawings/Self_driving_container-master/Drawings/Fifth_wheel/Fifth_wheel_assembly.SLDASM
85.8 x 35.5 x 80.0 mm
Fifth_wheel_mount
Fifth_wheel_disk
Fifth_wheel_kingpin
Fifth_wheel_axle

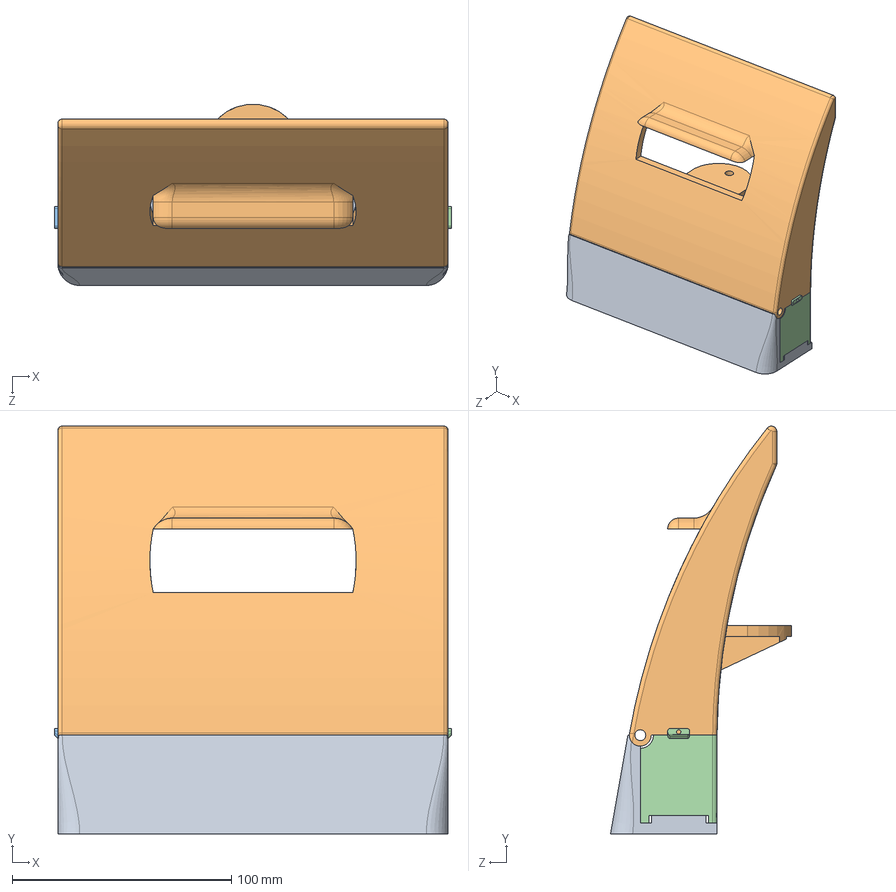
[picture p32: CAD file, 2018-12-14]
Backup_drawings/Self_driving_container-master/Drawings/Foldable_front/front assembly 2.SLDASM
181.0 x 185.9 x 82.6 mm
Foldable front base 2
foldable front flap 2
Foldable front side flap right 2
Foldable front side flap left 2

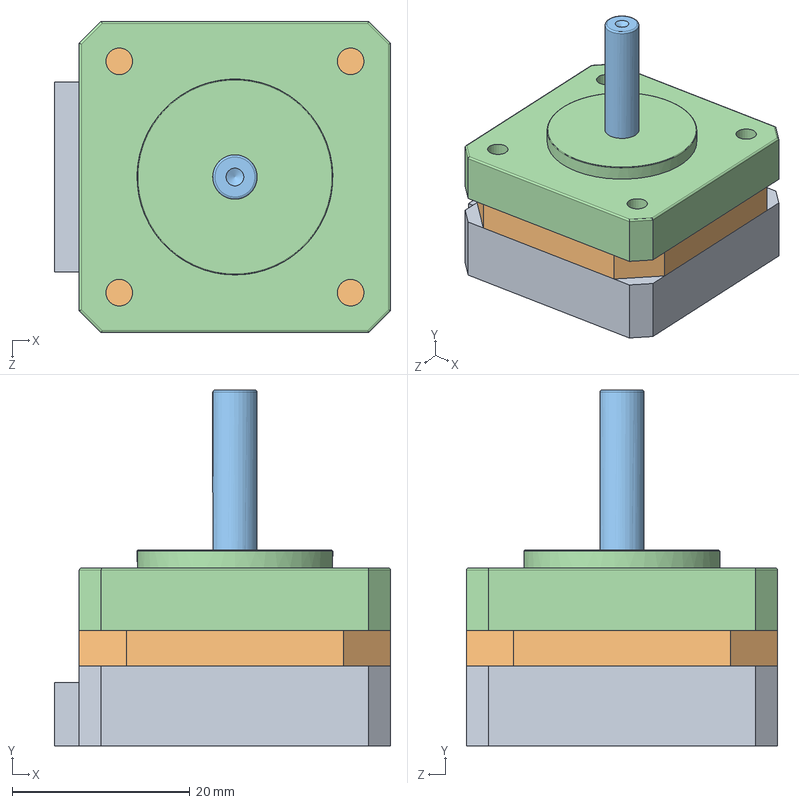
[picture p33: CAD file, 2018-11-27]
Dallas/docs/Drawings/Module/Nema 14/Stepper Nema14.SLDASM
37.8 x 40.0 x 35.0 mm
nema14_base
nema14_centro
nema14_eje
nema14_techo

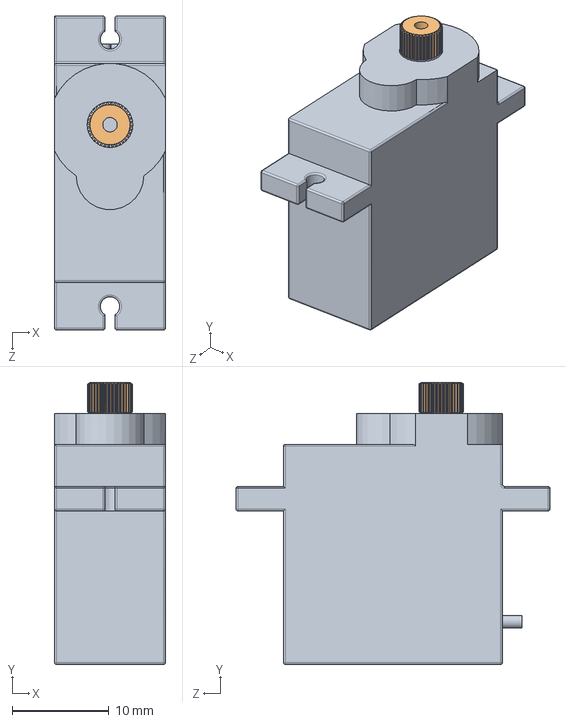
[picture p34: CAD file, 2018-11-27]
Dallas/docs/Drawings/Module/Servo/Servo motor.SLDASM
11.5 x 29.2 x 32.5 mm
TowerPro-SG90-Body
ServoFinalGear

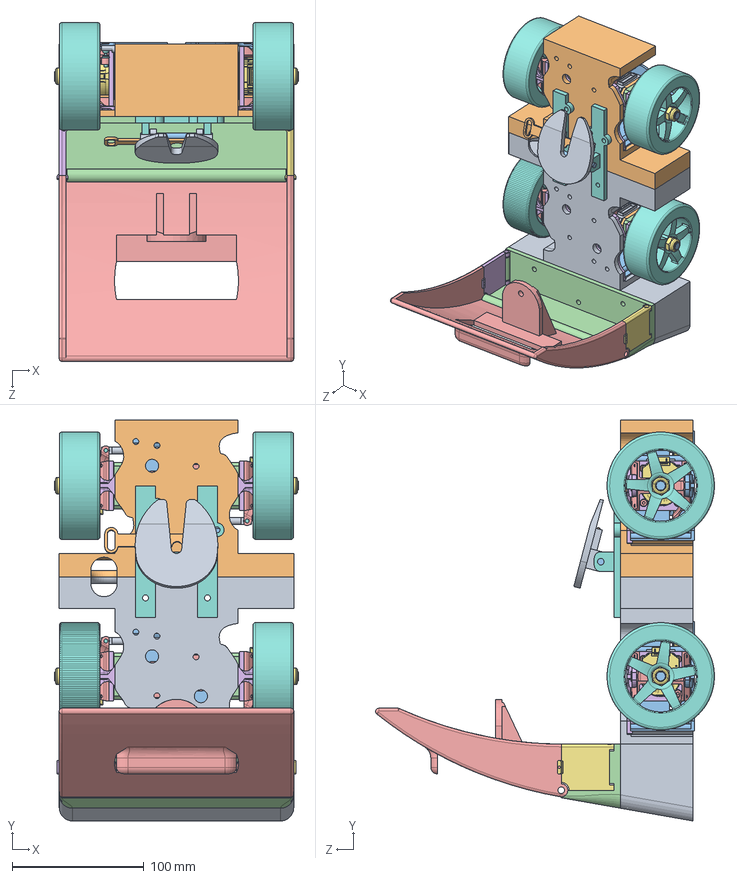
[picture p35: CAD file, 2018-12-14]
Backup_drawings/Self_driving_container-master/Drawings/Chassis/Chassis assembly 2.SLDASM
185.4 x 304.3 x 257.2 mm
Dolly chassis half 1
Dolly chassis half 2
Housing x 4
Bearing 12x8 x 8
Spindle x 4
Spindle base x 4
Encoder x 4
nema14_base x 4
nema14_centro x 4
nema14_eje x 4
nema14_techo x 4
TowerPro-SG90-Body x 4
ServoFinalGear x 4
Control arm x 4
Ball x 8
Joint x 8
Steering rod x 4
Wheel adapter x 4
Wheel spacer x 4
M3x5 din 7984 x 32
Housing lid x 4
M8 nut x 4
Wheel x 4
Fifth_wheel_mount
Fifth_wheel_disk
Fifth_wheel_kingpin
Fifth_wheel_axle
Foldable front base 2
foldable front flap 2
Foldable front side flap right 2
Foldable front side flap left 2

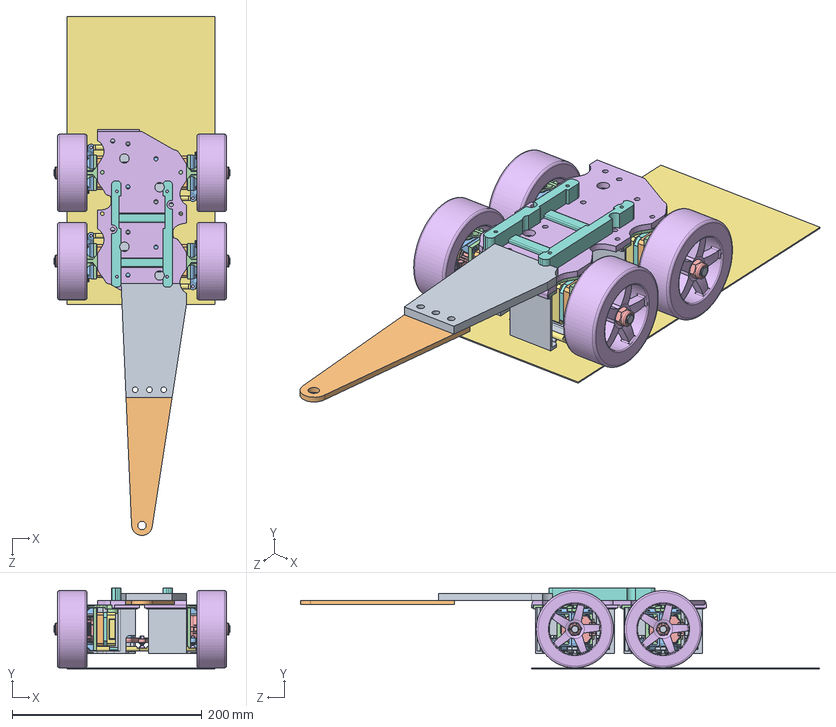
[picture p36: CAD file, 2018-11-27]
Dallas/docs/Drawings/Chassis/Assembly Dolley chassis.SLDASM
185.4 x 85.0 x 546.7 mm
Housing x 4
Bearing 12x8 x 8
Spindle x 4
Spindle base x 4
Encoder x 4
Wheel x 4
nema14_base x 4
nema14_centro x 4
nema14_eje x 4
nema14_techo x 4
TowerPro-SG90-Body x 4
ServoFinalGear x 4
Control arm x 4
Ball x 8
Joint x 8
Steering rod x 4
Wheel adapter x 4
Wheel spacer x 4
M3x5 din 7984 x 32
Housing lid x 4
M8 nut x 4
Dolly chassis
Fifth wheel adapter

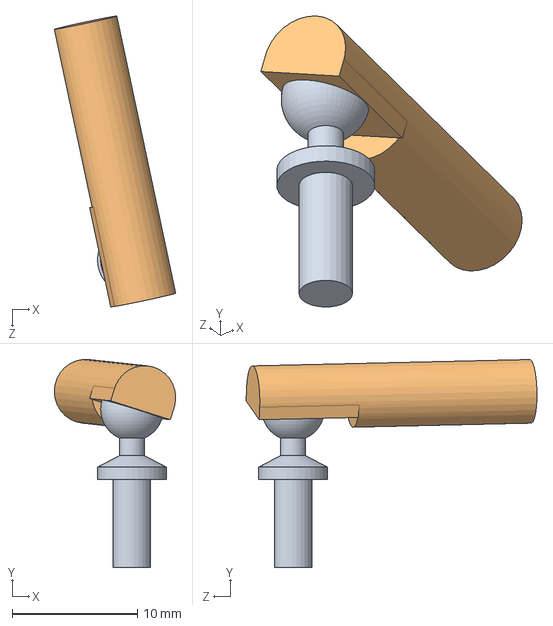
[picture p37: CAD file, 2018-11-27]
Dallas/docs/Drawings/Module/Ball joint/Ball joint assy.SLDASM
9.68 x 16.6 x 23.2 mm
Ball
Joint

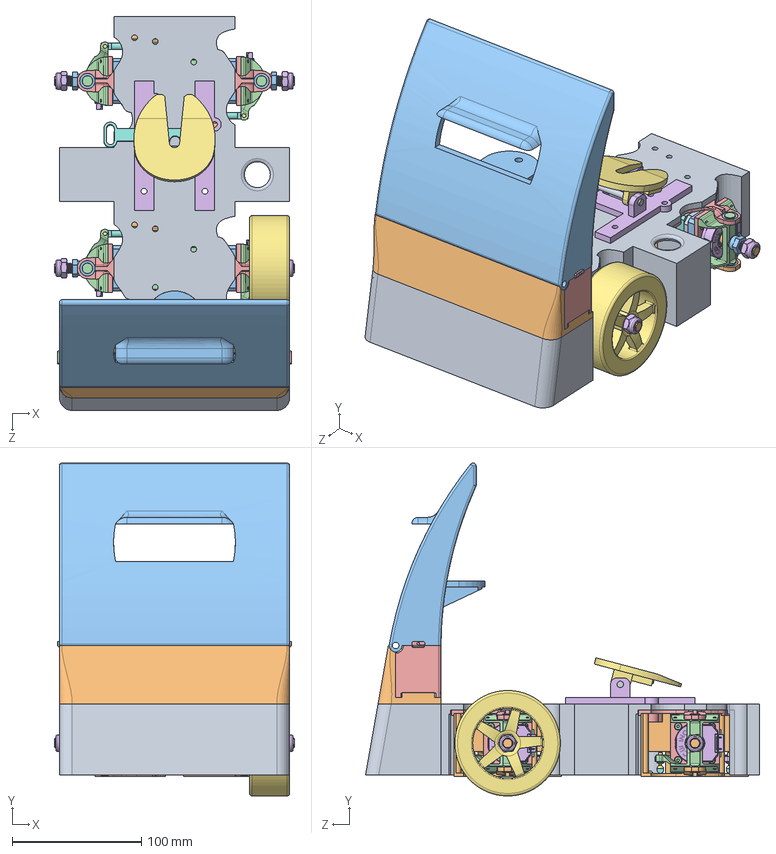
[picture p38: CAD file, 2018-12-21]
Drawings/Chassis/Chassis assembly 3.SLDASM
185.4 x 257.2 x 304.3 mm
Dolly chassis combined
Foldable front base 2
foldable front flap 2
Foldable front side flap right 2
Foldable front side flap left 2
Fifth_wheel_mount
Fifth_wheel_disk
Fifth_wheel_kingpin
Fifth_wheel_axle
Housing x 4
Bearing 12x8 x 8
Spindle x 4
Spindle base x 4
Encoder x 4
nema14_base x 4
nema14_centro x 4
nema14_eje x 4
nema14_techo x 4
TowerPro-SG90-Body x 4
ServoFinalGear x 4
Control arm x 4
Ball x 8
Joint x 8
Steering rod x 4
Wheel adapter x 4
Wheel spacer x 4
M3x5 din 7984 x 32
Housing lid x 4
M8 nut x 4

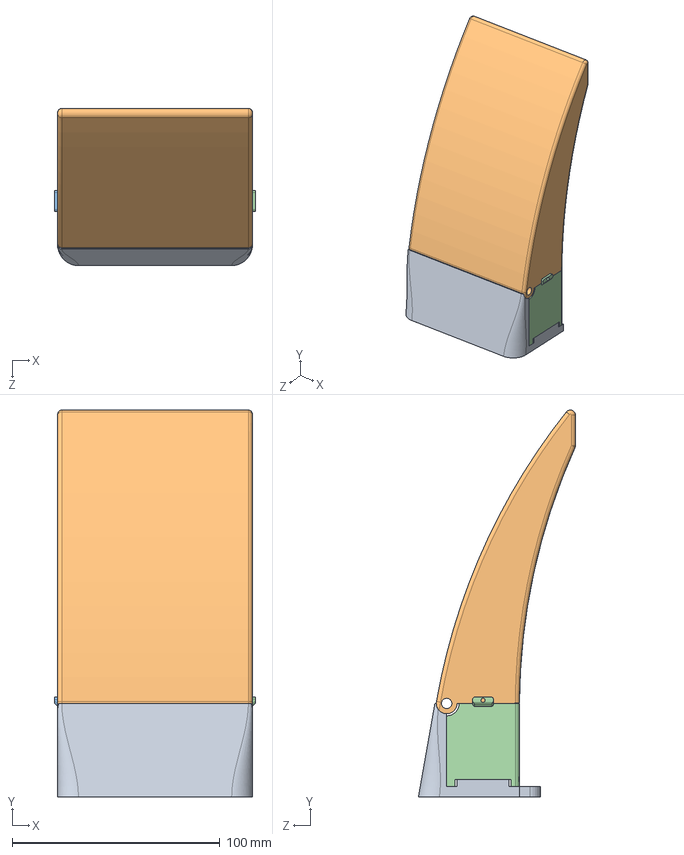
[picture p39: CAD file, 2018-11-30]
Backup_drawings/Self_driving_container-master/Drawings/Foldable_front/front assembly.SLDASM
96.7 x 186.1 x 75.6 mm
Foldable front base
foldable front flap
Foldable front side flap
Foldable front side flap left

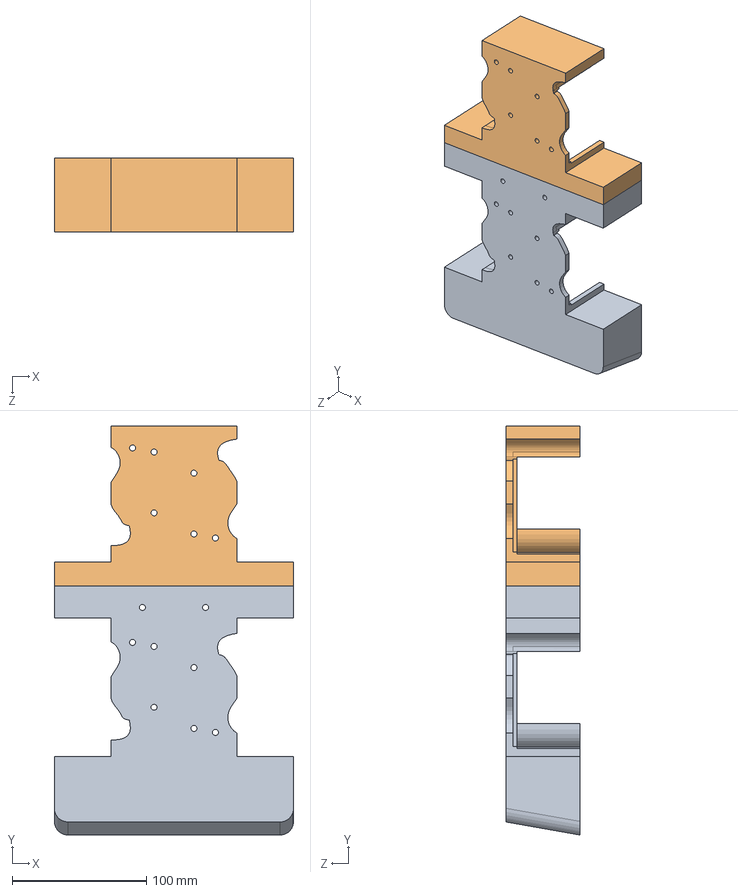
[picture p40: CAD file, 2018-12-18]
Drawings/Chassis/Assem1.SLDASM
178.0 x 304.3 x 55.0 mm
Dolly chassis half 1
Dolly chassis half 2

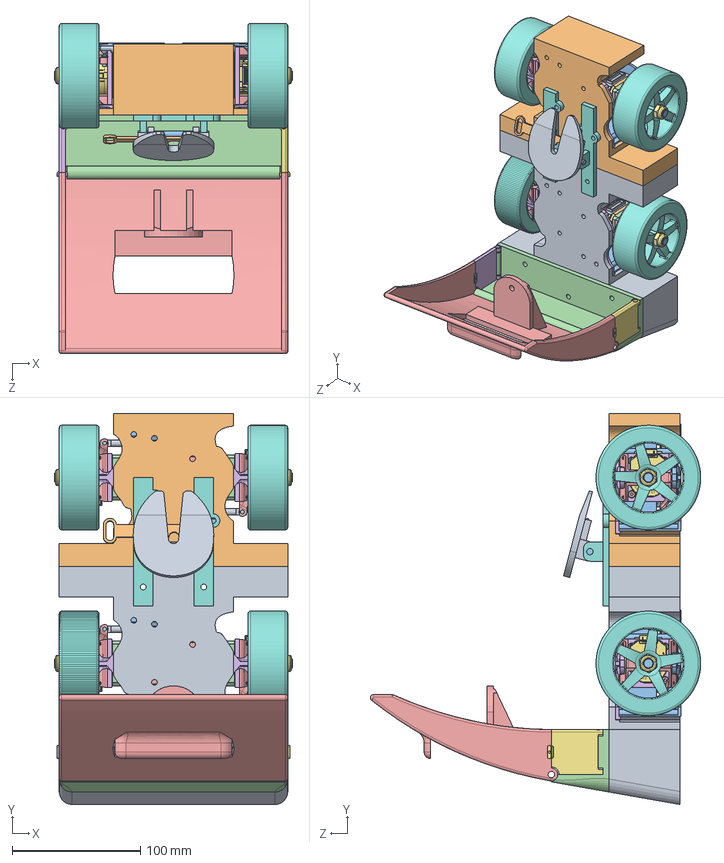
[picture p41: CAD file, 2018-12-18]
Drawings/Chassis/Chassis assembly 2.SLDASM
185.4 x 304.3 x 257.2 mm
Dolly chassis half 1
Dolly chassis half 2
Housing x 4
Bearing 12x8 x 8
Spindle x 4
Spindle base x 4
Encoder x 4
nema14_base x 4
nema14_centro x 4
nema14_eje x 4
nema14_techo x 4
TowerPro-SG90-Body x 4
ServoFinalGear x 4
Control arm x 4
Ball x 8
Joint x 8
Steering rod x 4
Wheel adapter x 4
Wheel spacer x 4
M3x5 din 7984 x 32
Housing lid x 4
M8 nut x 4
Wheel x 4
Fifth_wheel_mount
Fifth_wheel_disk
Fifth_wheel_kingpin
Fifth_wheel_axle
Foldable front base 2
foldable front flap 2
Foldable front side flap right 2
Foldable front side flap left 2

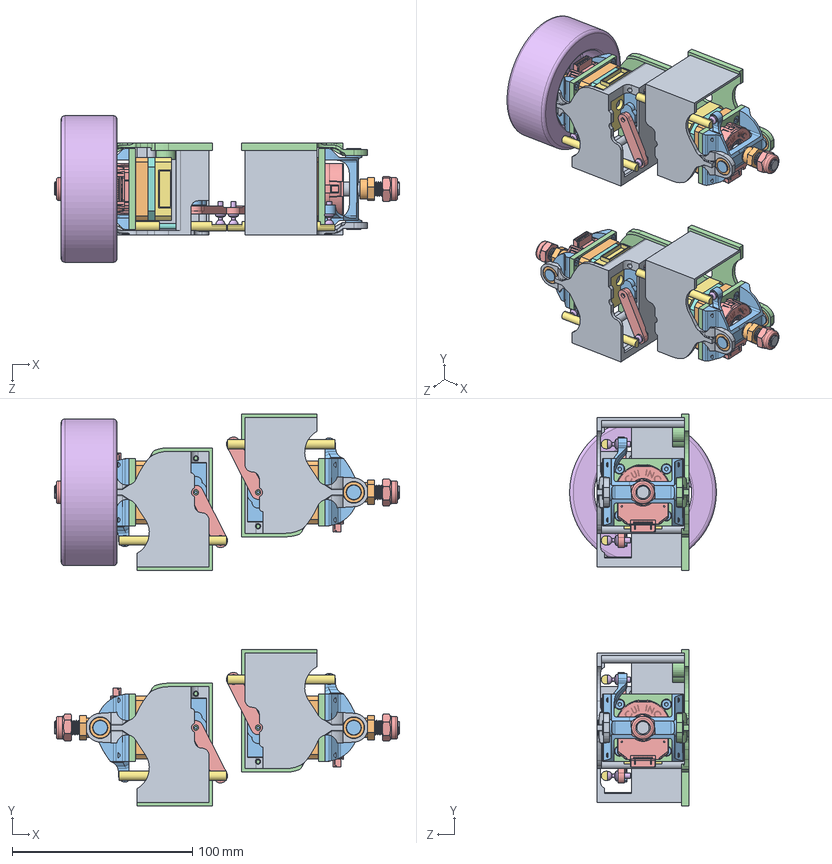
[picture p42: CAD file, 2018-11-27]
Backup_drawings/Self_driving_container-master/Drawings/Chassis/Chassis assembly.SLDASM
191.7 x 217.8 x 81.4 mm
Housing x 4
Bearing 12x8 x 8
Spindle x 4
Spindle base x 4
Encoder x 4
nema14_base x 4
nema14_centro x 4
nema14_eje x 4
nema14_techo x 4
TowerPro-SG90-Body x 4
ServoFinalGear x 4
Control arm x 4
Ball x 8
Joint x 8
Steering rod x 4
Wheel adapter x 4
Wheel spacer x 4
M3x5 din 7984 x 32
Housing lid x 4
M8 nut x 4

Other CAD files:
Drawings/Foldable_front/front assembly 2.SLDASM
Dallas/docs/Drawings/Module/Module Assembly.SLDASM
Drawings/Foldable_front/Assembly_front.SLDASM
Dallas/docs/Drawings/Chassis/Assembly Test chassis.SLDASM
Backup_drawings/Self_driving_container-master/Drawings/Chassis/Chassis assembly 2 - kopie.SLDASM
Backup_drawings/Self_driving_container-master/Drawings/Chassis/Chassis test.SLDPRT
Backup_drawings/Self_driving_container-master/Drawings/Chassis/Chassis.SLDPRT
Backup_drawings/Self_driving_container-master/Drawings/Chassis/Dolly chassis half 1.SLDPRT
Backup_drawings/Self_driving_container-master/Drawings/Chassis/Dolly chassis half 1.STL
Backup_drawings/Self_driving_container-master/Drawings/Chassis/Dolly chassis half 2.SLDPRT
Backup_drawings/Self_driving_container-master/Drawings/Chassis/Dolly chassis test.SLDPRT
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

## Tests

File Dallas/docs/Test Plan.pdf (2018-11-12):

HAN-AR
19-January-2017


| Document type Test Plan, Smart Quarter Vehicle
Author/Project group SMV. | Project: Smart modular vehicle. | Date 19-Jan-18
Document No | Issue 0.2 | Status Finished | Page No

# Test Plan

## Smart Quarter Vehicle

Status: Finished

Name | Student nr
William Marcelissen | 507428
Chris van der Spek | 561633
Gerran Jansma | 521675
Teun van den Burg | 530770

Document type

## Table of Contents

Document type

## 1 Introduction

All of the requirements are set up and approved by the client. To prove the requirements will be met at the end of the project several tests will be executed. These tests will prove the SMV is able to perform certain manoeuvres or meet certain specifications which are recorded in the set of requirements.
This document will describe a matching test for every requirement. This document also contains the preparation, resources and materials needed to successfully perform the test.

### 1.1 Test Definition

Req_ID | Requirement | Test method | Entrance Criteria
Measurement | Acceptance
Criteria

Status

Req_ID
The ID of the requirement this test case is linked to.

Requirement
The description of the requirement this test case is linked to.

Test Method
Description of the test.

Entrance Criteria
Criteria which have to be met before the test case can be executed.

Measurement
Description of the measurements which have to be conducted in order to prove that the system conforms to the respective requirement.

Acceptance Criteria
What are the boundaries where the measurement should be within, in order to classify this test-step as passed?

Status
Status can be either one of the following:

PRE Preliminary, not yet approved by team and client DEF Defined, approved by all stakeholders
REJ Test rejected, removed from scope
FAIL Test failed
PASS Test passed

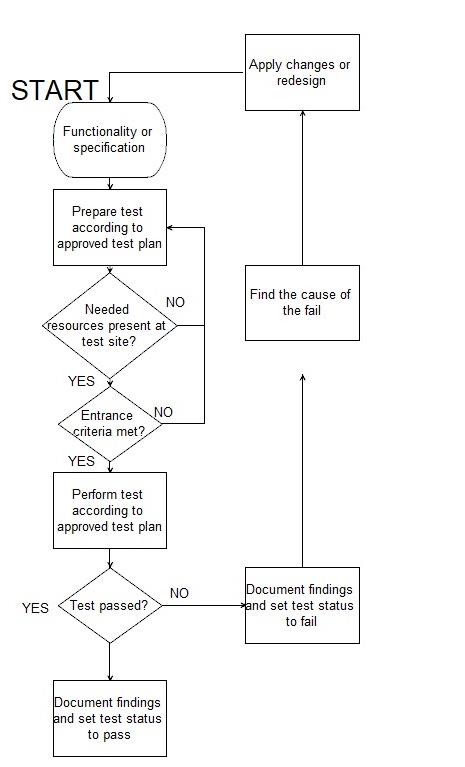
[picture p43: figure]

Document type

### 1.2 Test strategy

When the concerned product is ready and the entrance criteria are met the test can be performed. The test strategy will follow the path displayed in figure 1.

Figure 1 Test strategy

Document type

## 2 Test Preparation

### 2.1 Test Facilities & resources

Facility or resource | Test number | Time of occupation
Indoor space 3.5 by 6.5 [m] with smooth and clean surface | ALL TESTS | 2 weeks
Master computer and (drone) camera | ALL TESTS | 2 weeks
PC to program SMV | ALL TESTS | 2 weeks
Masking tape | TEST 1 | 3 days
Tape measure | TEST 1; TEST 6; TEST 9; TEST 12; TEST 13; | 4 days
Protractor | TEST 5; TEST 7; TEST 8 | 2 days
Scope | TEST 3; TEST 4 | 2 days
Weight of 3[kg] | TEST 16 | 1 day
Calliper | TEST 16 | 1 day
Stopwatch | TEST 6; TEST 10 | 2 days

### 2.2 Responsibilities during test

During the test period Chris van der Spek is head of testing. Therefore Chris van der Spek is responsible for the test, test equipment, surroundings and the SMV. But tests can be performed by different project group members.

### 2.3 Conditions to be met before starting the test phase

Before entering the test phase the product has to be finished. This means all components are assembled and the software is programmed. Also external equipment such as the existing master computer must be running and be connected to the SMV so it can send the predefined path to the SMV’s microcontroller.

When these conditions are met the entrance criteria ‘System is running’ is met.

Document type

## 3 Test Cases

Req_ID | Test method | Entrance Criteria | Stimuli | Measurement | Acceptance Criteria | Status
FR01 | The SMV must be able to follow a predefined path by communicating to an existing master computer. | Let the SMV follow a predefined path by communicating to the master computer. | Master computer gives SMV the command to follow the predefined path. | The predefined path will be outlined¹⁾. A visual inspection will conclude if the SMV stays between boundaries | SMV must be between the boundaries of the road¹⁾ in the predefined path which will be 0.32 [m] wide. | PRE
FR01.1 | Smart modules must be able to steer via a predefined path.(See appendix II) | Visual control if two modules steer and let the SMV follow a path (within certain tolerances) with multiple corners both to the left and to the right. | Master computer gives SMV the command to follow the predefined path. | The predefined path will be outlined¹⁾. A visual inspection will conclude if the SMV stays between boundaries | SMV must be between the boundaries of the road¹⁾ in the predefined path which will be 0.32 [m] wide. | PRE
FR02 | Let the SMV, with four connected modules, run the predefined path | - System must be running - Path must be known - Path must be set out on the floor | - Start the system | - Visual, see if SMV follows predefined path | - SMV must stay in lane [1] | PRE
FR02.1 | Lock modules by software. Check if they are locked. | - System must be running | - Lock the modules via software | - See if modules are locked. | Wheels are locked | PASS
FR03 | The chassis must include a battery to run a predefined path | Let the SMV run the predefined path on 1 charge. | Master computer gives SMV the command to follow the predefined path | Visual inspection if the SMV succeeds in completing path on a battery charge | SMV drives the predefined path wireless | PASS
FR04 | Visual inspection, retrieve RPM data. | - Connect scope or PC to driver motor. | - None | - Turn driver motor, see if rpm signal appears on scope. | - Signal should be present and clear. | PASS
FR05 | Visual inspection, retrieve steering angle data. | - Connect scope or PC to steering motor. - SMV must be connected to PC to set a steering angle | - Set steering angle | - Create a steering angle and see if signal appears. | - Signal should be present and clear. | PASS
PR01 | Drive one lap wireless to confirm the communication is wireless. | The SMV will not be wired and not physically connected to the master computer. | Starting the protocol of driving one lap. | Visual, see if the SMV will drive one lap wireless. | When the SMV completes the predefined as desired. | PASS
PR02 | Calculate the steering angle with Ackermann principal. Use this steering angle for the SMV as input and measure it. | To entrance the test it needs to be applied. | Use the calculated steering angle as input for the SMV. | Draw the angles of the steering from the SMV on the ground and draw the ‘’Ackermann principal’’. Measure it and compare it. | When the SMV measurement is between +/- 5 degrees with the calculated angle. | PRE
PR03 | Measure the speed average by travel distance and time | System running | Start the SMV to drive. | Test track with the total distance. Measure the time with an stopwatch. | When the SMV reaches a speed of 0.1 [m/s] | PASS
PR04 | Put the 30 degrees steering angle in the system of the SMV and | System running. | Start the SMV to get the input steering angle. | Visual, draw the angles of the steering from | The steering angle is the same as the | PASS

Document type

| measure it. | | | the SMV on the ground and measure the angle. | input steering angle.
PR04.1 | Put the 50 degrees steering angle in the system of the SMV and measure it. | System running. | Start the SMV to get the input steering angle. | Visual, draw the angles of the steering from the SMV on the ground and measure the angle. | The steering angle is the same as the input. | FAIL
PR04.2 | Make a turn with a turning radius of 0.9[m] | System running. | Start the SMV to drive. | Draw starting position. SMV will turn around and draw the end position. Measure this. | When the turning radius is equal to 0.9[m] or smaller. | PASS
PR05 | Drive the predefined path for one hour | System running. | Start the SMV to drive. | Timing from start till an hour. | When the SMV has been driving at least for an hour. | PRE
PHR01 | Visual inspection | - | | Identity check | Approved when wheel are the same | FAIL
PHR02 | Measure the distance between the left outside wheels tot the right outside wheels | -No steering angle is applied | | Distance | Distance ≤ 17.86cm | PASS
PHR03 | Measure the length of the modules. | - | - | Distance | Distance ≤ calculated dimension(set of requirements) | PASS
PHR04 | Visual inspection | - | - | Identity check | Approved when connections are standardized | PASS
PHR05 | Visual inspection, check of modules are rigid after 15 minutes of operation | -Vehicle drives the predefined path for 15 minutes | Start the SMV time | Check Structural rigidity by checking the mounting hardware | No mounting hardware has come lose after operation | PASS
PHR06 | Apply a three kilogram weight in the middle of the vehicle and measure the bending in the mid-point of the platform | -Vehicle is in stationairy position -No steering angle is applied -Only four modules have to be installed | Apply a weight | Bending in the middle of the vehicle | Bending ≤ 10mm | PRE
PHR07 | NA | - | - | - | - | -
PHR07.1 | NA | - | - | - | - | -
1) see appendix: Road information

Document type

## 4 Test forms

Test ID | TEST 1 (FR01; FR01.1; FR02; FR03; PR01)
Necessary resources | - Masking tape - Tape measure - Indoor space of 3.5 by 6.5 [m] with smooth and clean surface - Master computer and (drone) camera - PC to program SMV
Entrance criterium #1 | System is running²⁾
Entrance criterium #2 | Path is set out
Entrance criterium #3 | Path is known by master computer
| Measurement
Test Passed? | YES
Comments: | -
Test conducted by: | Chris,Gerran,Teun,William
Date: | 22-12-2017
Test ID | TEST 2 (FR02.1)
Necessary resources | - PC to program SMV
Entrance criterium #1 | System is running²⁾
| Measurement
Test Passed? | YES
Comments: | -
Test conducted by: | Chris
Date: | 20-12-2017
Test ID | TEST 3 (FR04)
Necessary resources | - Scope
Entrance criterium #1 | Connect driver motor RPM sensor to scope
| Measurement
Test Passed? | YES
Comments: | -
Test conducted by: | Chris
Date: | 20-12-2017
Test ID | TEST 4 (FR05)
Necessary resources | - Scope
Entrance criterium #1 | Connect steering motor RPM sensor to scope
| Measurement
Test Passed? | YES
Comments: | -
Test conducted by: | Chris
Date: | 20-12-2017

Document type

Test ID | TEST 5 (PR02)
Necessary resources | - Protractor - PC to program SMV
Entrance criterium #1 | System is running²⁾
| Measurement
Test Passed? | YES
Comments: | Used radius of 0.34 m
Test conducted by: | Chris
Date: | 20-12-2017
Test ID | TEST 6 (PR03)
Necessary resources | - Measuring tape - Stopwatch - PC to program SMV - Indoor space of 3.5 by 6.5 [m] with smooth and clean surface
Entrance criterium #1 | System is running²⁾
| Measurement
Test Passed? | YES
Comments: | Precise driving
Test conducted by: | Chris, William, Gerran, Teun
Date: | 12-12-2017
Test ID | TEST 7 (PR04)
Necessary resources | - Protractor - PC to program SMV
Entrance criterium #1 | System is running²⁾
| Measurement
Test Passed? | YES
Comments: | -
Test conducted by: | Chris
Date: | 12-12-2017
Test ID | TEST 8 (PR04.1)
Necessary resources | - Protractor. - PC to program SMV
Entrance criterium #1 | System is running²⁾
| Measurement
Test Passed? | NO
Comments: | Max steering angle is 40 degrees
Test conducted by: | Chris
Date: | 12-12-2017

Document type

Test ID | TEST 9 (PR04.2)
Necessary resources | - Measuring tape - PC to program SMV - Indoor space of 3.5 by 6.5 [m] with smooth and clean surface
Entrance criterium #1 | System is running²⁾
| Measurement
Test Passed? | YES
Comments: | SMV can make quite smaller angles, a radius of 0,9 meters is easily reached
Test conducted by: | Chris, William, Gerran, Teun
Date: | 12-12-2017
Test ID | TEST 10 (PR05)
Necessary resources | - Stopwatch. - Masking tape - Tape measure - Indoor space of 3.5 by 6.5 [m] with smooth and clean surface - Master computer and (drone) camera - PC to program SMV
Entrance criterium #1 | System is running²⁾
| Measurement
Test Passed? | YES
Comments:
Test conducted by: | Chris, William, Gerran, Teun
Date: | 22-12-2017
Test ID | TEST 11 (PHR01)
Necessary resources | - Visual inspection
Entrance criterium #1 | The used RC truck wheel must be available
| Measurement
Test Passed? | NO
Comments: | Design was not possible with truck wheel due to small in wheel space for hub
Test conducted by: | Teun
Date: | 12-12-2017
Test ID | TEST 12 (PHR02)
Necessary resources | - Measuring tape
Entrance criterium #1 | No steering angle is applied
| Measurement
Test Passed? | YES
Comments: | Depending on how tight the wheels are locked, 17,86 cm is reached
Test conducted by: | Chris
Date: | 12-12-2017

Document type

Test ID | TEST 13 (PHR03)
Necessary resources | - Measuring tape
Entrance criterium #1
| Measurement
Test Passed? | YES
Comments: | 69 mm
Test conducted by: | Teun
Date: | 12-12-2017
Test ID | TEST 14 (PHR04)
Necessary resources | - Visual inspection
Entrance criterium #1
| Measurement
Test Passed? | YES
Comments:
Test conducted by: | Chris
Date: | 12-12-2017
Test ID | TEST 15 (PHR05)
Necessary resources | - Visual inspection - Masking tape - Tape measure - Indoor space of 3.5 by 6.5 [m] with smooth and clean surface - Master computer and (drone) camera - PC to program SMV
Entrance criterium #1 | - Vehicle has driven the predefined path for 15 minutes
| Measurement
Test Passed? | YES
Comments:
Test conducted by: | Chris
Date: | 12-12-2017

Document type

Test ID | TEST 16 (PHR06)
Necessary resources | - A three kilogram weight
Entrance criterium #1 | - Vehicle is in stationary position - No steering angle is applied - Only four modules have to be installed
| Measurement
Test Passed? | YES
Comments:
Test conducted by: | Chris
Date: | 8-1-2018
2) According to chapter 2.3

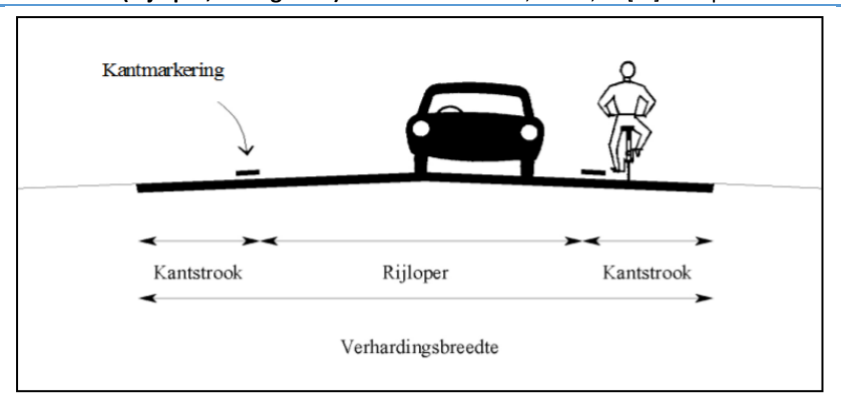
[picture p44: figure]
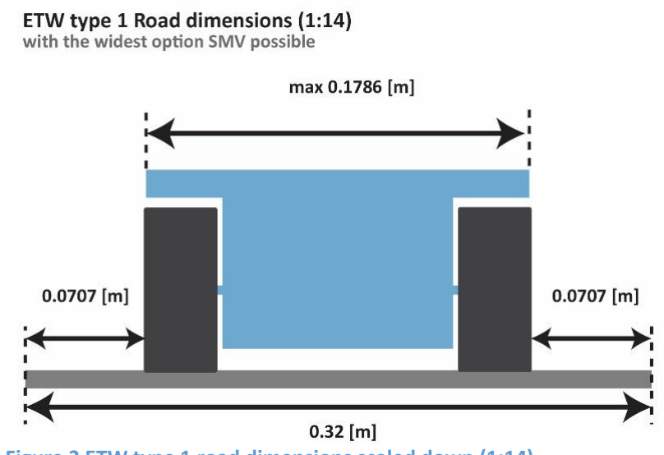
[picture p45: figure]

Document type

## Appendix: Road information

Because of the fact that the SMV will be a scale 1:14 project that is compared with the dimensions of a real semi-truck, the road is also scaled 1:14. The justification of the road dimensions are based on the stated information released by CROW¹⁾

Table 1 guidelines ETW public roads outside build-up areas by CROW

| ETW type I | ETW type II
Maximum allowed speed | 60 [km/h] | 60[km/h]
Amount of lanes | One | One
Total width (Verhardingsbreedte, see figure 2) | 4,50 – 6,20 [m] | <4,50 [m]
Width lane (Rijloper, see figure 2) | 3,00 – 4,50 [m] | Equals to total width

For the predefined path dimensions, the ETW type I dimensions are chosen with the maximum lane width of 4,50 [m]. The maximum dimension is chosen to give the SMV as much space as possible between the recommended road dimensions. Figure 3 clarifies the road dimensions when scaled down to scale 1:14

Sources:

Figure 2 definitions road sections by CROW in Dutch

Figure 3 ETW type 1 road dimensions scaled down (1:14)

Document type

Unknown, CROW. (2013). Kantstroken op erftoegangswegen buiten de bebouwde kom. 02-10-2017. https://www.swov.nl/file/13352/download?token=S9pB6p0N

1) CROW is a knowledge organization in the infrastructure, traffic, and transport working field. CROW recommendations and guidelines

are not stated in the dutch law, but the dutch road operators do use the CROW recommendations and guidelines to substantiate their decisions to the Dutch government.

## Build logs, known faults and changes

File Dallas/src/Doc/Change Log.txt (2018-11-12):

# Change Log
All notable changes to the HANcoder project will be documented in this file

## Version 0.4
- Changed from Sourcery Codebench lite to the GNU ARM Embedded Toolchain
- Added support for Matlab 2014b, 2015a, 2015b, 2016a & 2016b
- Added Analog Ouputs (D10 and D13)
- Changed naming of the output pins: only the connector name is used (PG - 3 = pin 3 on connector PG)
- UDP blocks have been added
- CANopen Node blocks are added but not extensively tested
- CANopen Client blocks have been deleted because of several issues with the blocks
- RAM blocks have been removed, it is better to use the Simulink Data Store blocks
- Java is no longer required. (ASAP2 post processing is now done in Matlab)
- An auto flash function is added that allows the user to automatically start MiroBoot after a succesful build
- A function is added which automatically adds signals and parameters for HANtune
- The A2L file is now placed in the same directory as the model
- The timing of the E407 is fixed. (It is no longer off by 4%)
- The CAN receive blocks now output the last received values when no new message was received.

Warning:
- Due to a change in structure all HANcoder blocks in older models must be replaced!

## Version 0.5
- Changed template makefile to accept non-8dot3 names (short names like C:/Progra~1)
- Increased size of additional stack in the Base Sample Time blocks
-

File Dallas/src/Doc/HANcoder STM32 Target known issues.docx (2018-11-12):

## HANcoder STM32 Target known issues v0.5

### The following bugs are known for all HANcoder targets:

- None at the moment

### The following issues are known in the HANcoder E407 Target:

- When pin D1 on connector 3 is chosen as digital input CANbus 1 no longer works. CANbus 2 however keeps working
- When pin D1 on connector 3 is chosen as an output both CANbus 1 and 2 no longer work.
- Because of a mistake on the E407 board the analog inputs on the E407 have quite some noise, about 25 LSB of the 4096. (The analog ground is not connected properly)
- When a connection with HANtune is made over TCP/IP. The E407 is not able to receive UDP messages. As soon as the connection with HANtune is broken the UDP receive block works again. This bug is also known to cause the controller to crash, it should therefore be avoided. It is possible to use HANtune over USB or CAN in combination with the UDP receive block.

### The following bugs are known in the HANcoder Olimexino Target:

- When timer 4 is used in the ‘Timer input get block’ the CAN communication stops working.

### The following bugs are known in the HANcoder P405 Target:

- The software for the P405 has not been tested extensively.

If any more issues are found please send the bug report to: HANcoder@han.nl or Jason.vanKolfschoten@han.nl

Sjabloon3, JvH, 23/10/2016

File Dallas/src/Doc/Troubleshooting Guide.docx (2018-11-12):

| HANcoder STM32 Trouble Shooting Guide

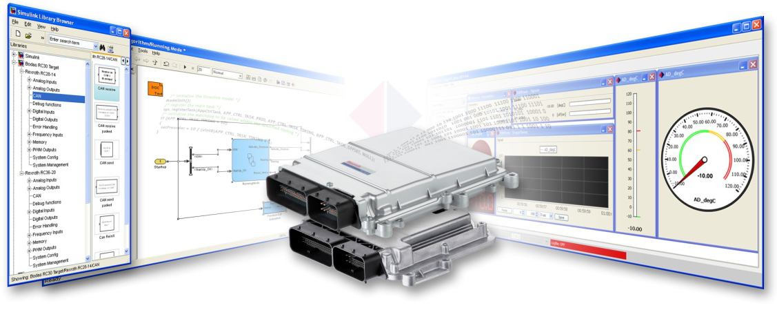
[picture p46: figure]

Version 0.5 10/23/2016 | Trouble Shooting Guide
| A guide containing the solutions to previously encountered problems

# HANcoder STM32 Trouble Shooting Guide

Trouble Shooting Guide

# Versioning

Nr | Date | Person | Changes | Status
0. 1 | 28-09-2016 | J. van Kolfschoten | First version | Concept
0.5 | 23-10-2016 | J van Kolfschoten | Updated to the new blockset version | Finalized

# Introduction

In this document the solution to previously encountered problems can be found.

To get personal help and to keep this document up to date, please contact the Jason van Kolfschoten: Jason.vanKolfschoten@han.nl, if you encounter a problem which is not documented here.

# 1 Problems during installation

## 1.1 USB driver installation with Zadig.exe fails

When the openblt.cfg file is in a path with a long name the installation can fail. Switch to Advanced mode in the Options menu of the program to check is the Openblt.cfg file can be opened.

# 2 Problems in the model

## 2.1 The project contains ‘Unresolved Link’-blocks

Possible causes & solutions

This probably means the paths haven’t been set correctly. Make sure the current folder of Matlab is the same folder as where the model file (.slx) is located. Close and reopen the model file once you have set the correct directory in Matlab, you should see the directory ‘blockset’.

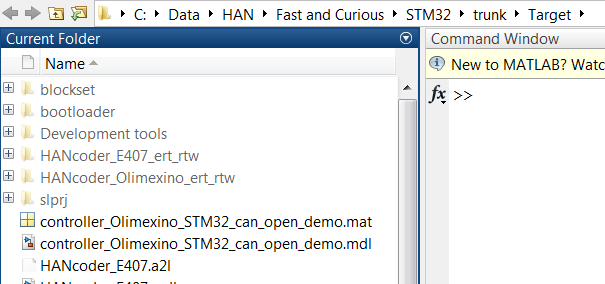
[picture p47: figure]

Alternatively to reopening the model you can run the m-script librarySetup.m after redirecting Matlab to the correct directory.

# 3 Problems during the build procedure

“### Real-Time Workshop build procedure for model: 'controller_Olimexino_STM32' aborted due to an error.”

There are a few possible errors with multiple causes during the build procedure

## 3.1 Gmake: *** [model.obj] Error 1

After pressing the ‘Build model’ button or Ctrl+b the following error appears:

### Compiling model.c -o model.obj

arm-none-eabi-gcc: error: target\trunk\Target\controller_Olimexino_STM32_ert_rtw: No such file or directory

arm-none-eabi-gcc: error: target\trunk\Target: No such file or directory

gmake: *** [model.obj] Error 1

### Real-Time Workshop build procedure for model: 'controller_Olimexino_STM32' aborted due to an error.

>>

Possible problem:

There is a space in the folder where the model resides. Because of this the compiler cannot find the specified folder. See above: the compiler is directed to ‘target\trunk\Target\controller_Olimexino_STM32_rtw’, this path is missing the ‘C:\...” The full path was: ‘C:\STM32 target\trunk\Target\controller_Olimexino_STM32_rtw’.

## 3.2 Gmake: *** [<modelname>.obj] Error 1

After pressing the ‘Build model’ button (Ctrl+b) the following error appears:

### Compiling controller_Olimexino_STM32.c -o controller_Olimexino_STM32.obj

In file included from controller_Olimexino_STM32.c:17:0:

controller_Olimexino_STM32.h:22:20: fatal error: timein.h: No such file or directory

#include "timein.h"

^

compilation terminated.

gmake: *** [controller_Olimexino_STM32.obj] Error 1

### Real-Time Workshop build procedure for model: 'controller_Olimexino_STM32' aborted due to an error.

Possible problem:

The ‘Simulation cache folder’ and ‘Code generation folder’ in the Simulink Preferences are not empty and not directing to the target folder

Solution:

Empty the fields ‘Simulation cache folder’ and ‘Code generation folder’ in Simulink Preferences.

## 3.3 Gmake: *** [clean] Error 2

After pressing the ‘Build model’ button (Ctrl+b) the following error appears:

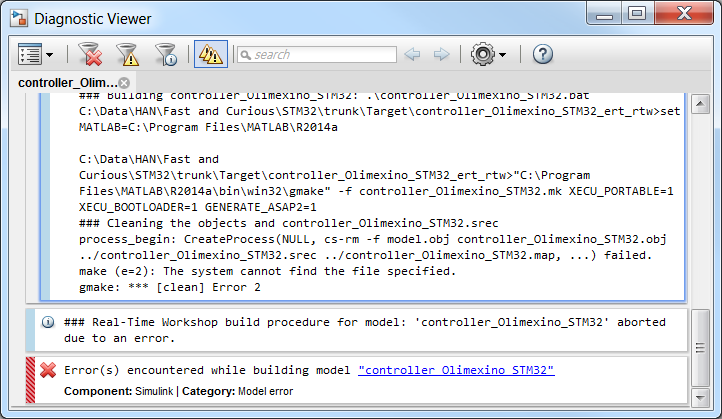
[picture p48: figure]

Possible problem 1: The PATH to the GNU ARM embedded toolchain is not set correctly in the environment variables.

Solution: Go to Environment Variables by right clicking ‘My Computer’ and selecting properties -> Click ‘Advanced system settings’ -> click ‘Environment Variables …’ Select the PATH variable and click edit to check/correct the folder location to:

‘C:\Program Files\GNU Tools ARM Embedded\5.4 2016q2\bin’.

Possible problem 2: MATLAB has not been run as administrator.

Solution: Run MATLAB as administrator

## 3.4 Error building model: dialog out of screen boundaries

### Problem:

When starting the build procedure a dialog from HANcoder appears in the task bar but is not visible on the screen.

Solution: This is an Error that’s in MATLAB itself. There has to be a ‘startup m-file’ in the beginning file of MATLAB to prevent this from happening.
Startup MATLAB, in the left section of the program, the current folder section, the file is shown which MATLAB starts with. Make a new script ( in the upper left corner ).

Copy paste the following script in the m-file and call this file startup

figure('units','pixels','position',[680 678 560 420]);

close all;

set(0,'defaultfigureposition',[680 678 560 420]);

clc

From now on, MATLAB will execute this script first when it is started. The dialog will appear in the screen from now on.

# 4 Problems with flashing

## 4.1 Error during flash procedure with MicroBoot ‘Could not clear memory..’

When trying to flash the STM32 Olimexino via CAN or USB the following error appears:

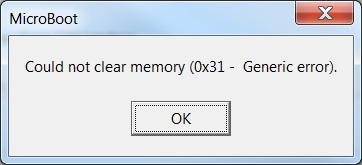
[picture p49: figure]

Problem: The model was not set up for use with the bootloader via CAN

Solution: Set ‘HANcoder_BOOTLOADER=1’ at the make command in the configuration parameters of the model. See below..

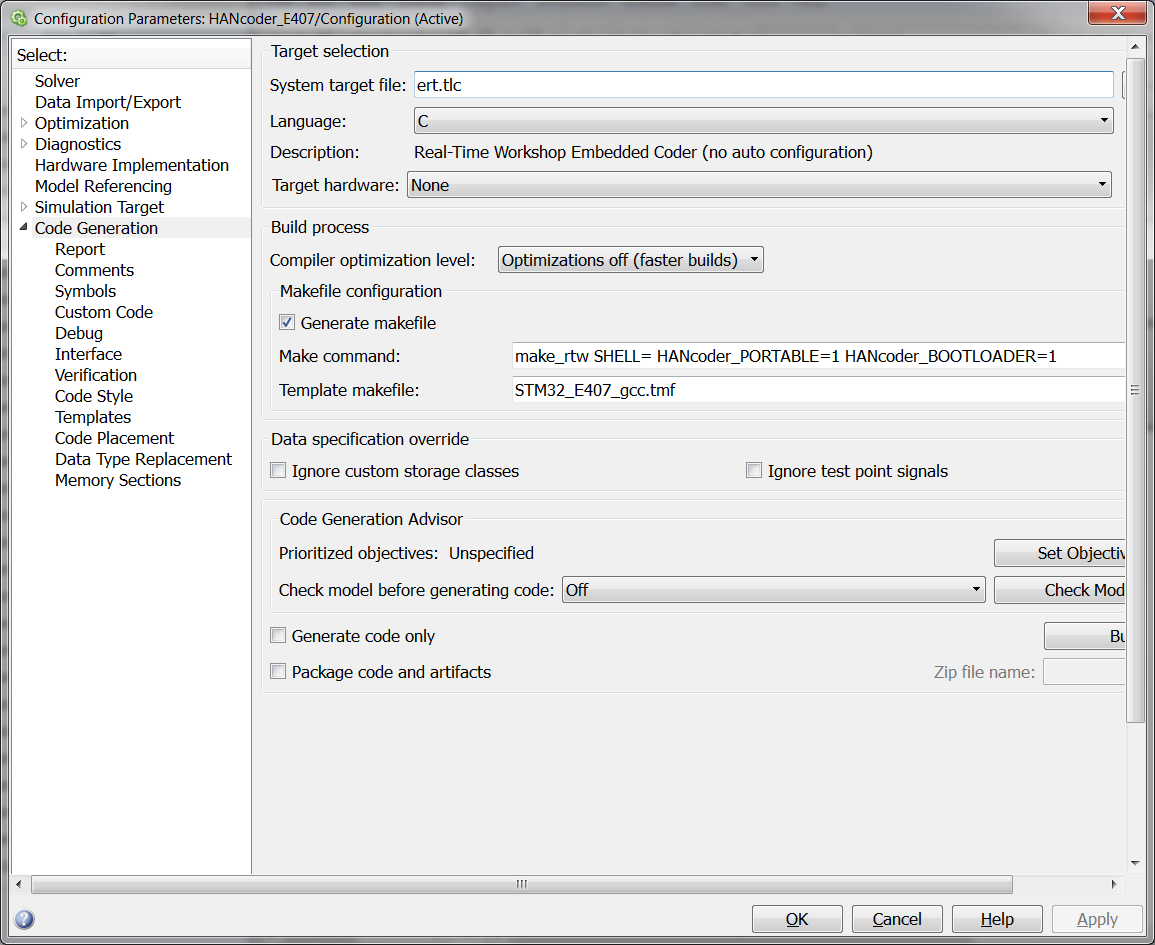
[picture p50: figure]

HANcoder STM32 Trouble Shooting Guide, v0.5

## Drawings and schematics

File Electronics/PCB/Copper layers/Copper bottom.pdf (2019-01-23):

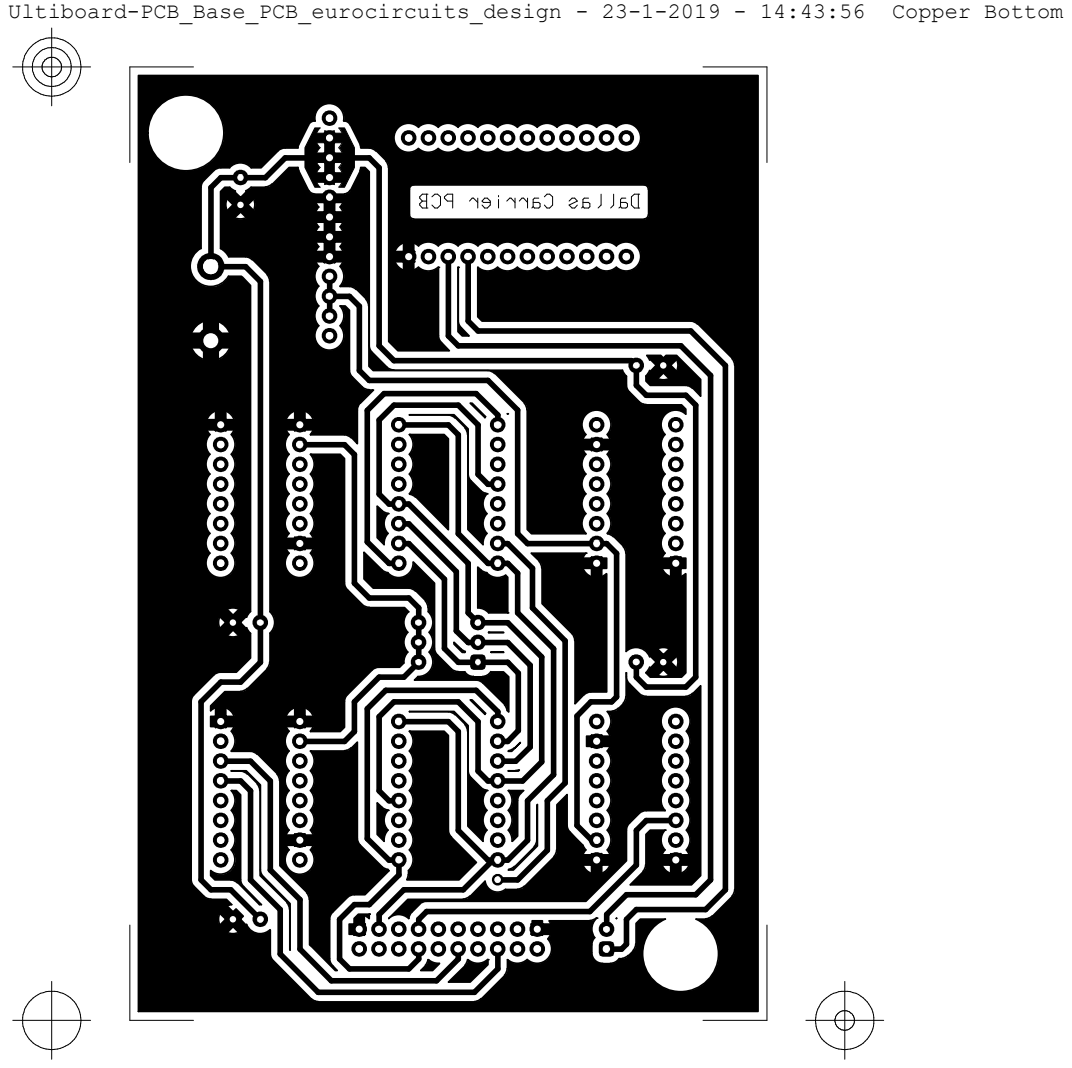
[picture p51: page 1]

Ultiboard-PCB_Base_PCB_eurocircuits_design - 23-1-2019 - 14:43:56 Copper Bottom

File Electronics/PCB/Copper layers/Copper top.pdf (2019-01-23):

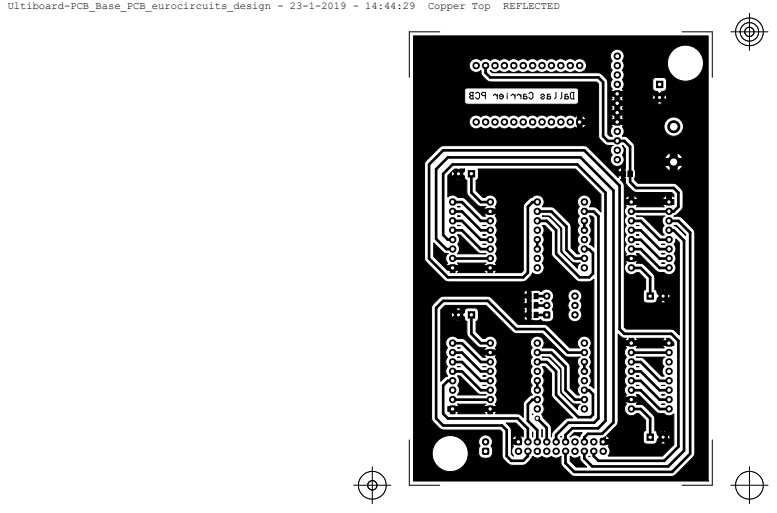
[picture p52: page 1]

Ultiboard-PCB_Base_PCB_eurocircuits_design - 23-1-2019 - 14:44:29 Copper Top REFLECTED

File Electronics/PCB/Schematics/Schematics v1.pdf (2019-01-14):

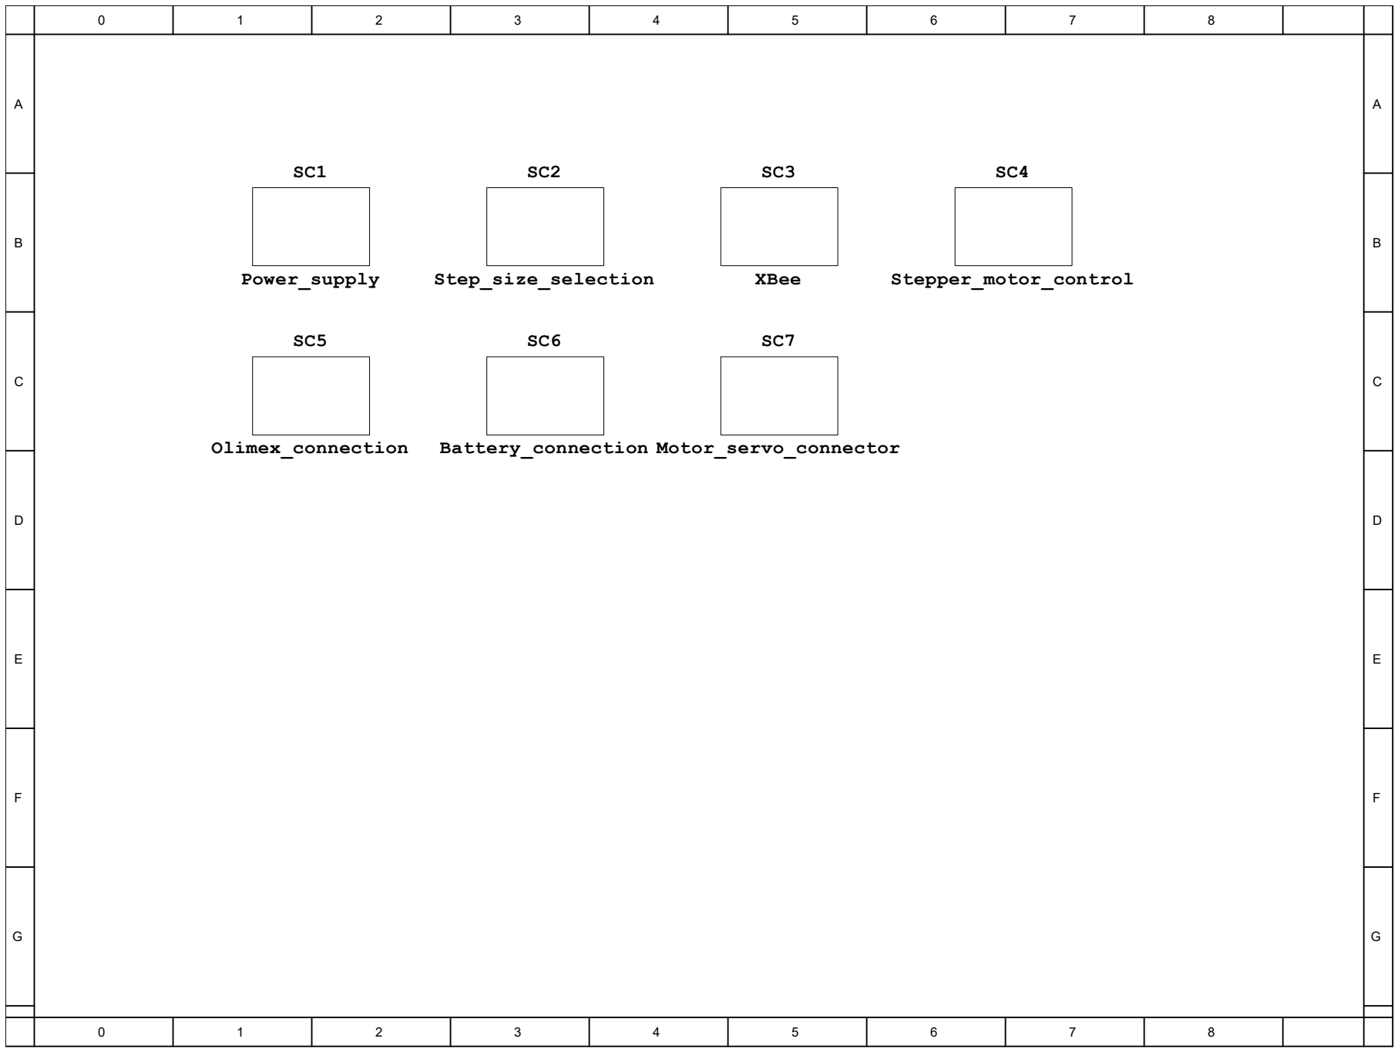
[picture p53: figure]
Step_size_selection; Power_supply; XBee; Stepper_motor_control; Olimex_connection; Battery_connection; Motor_servo_connector
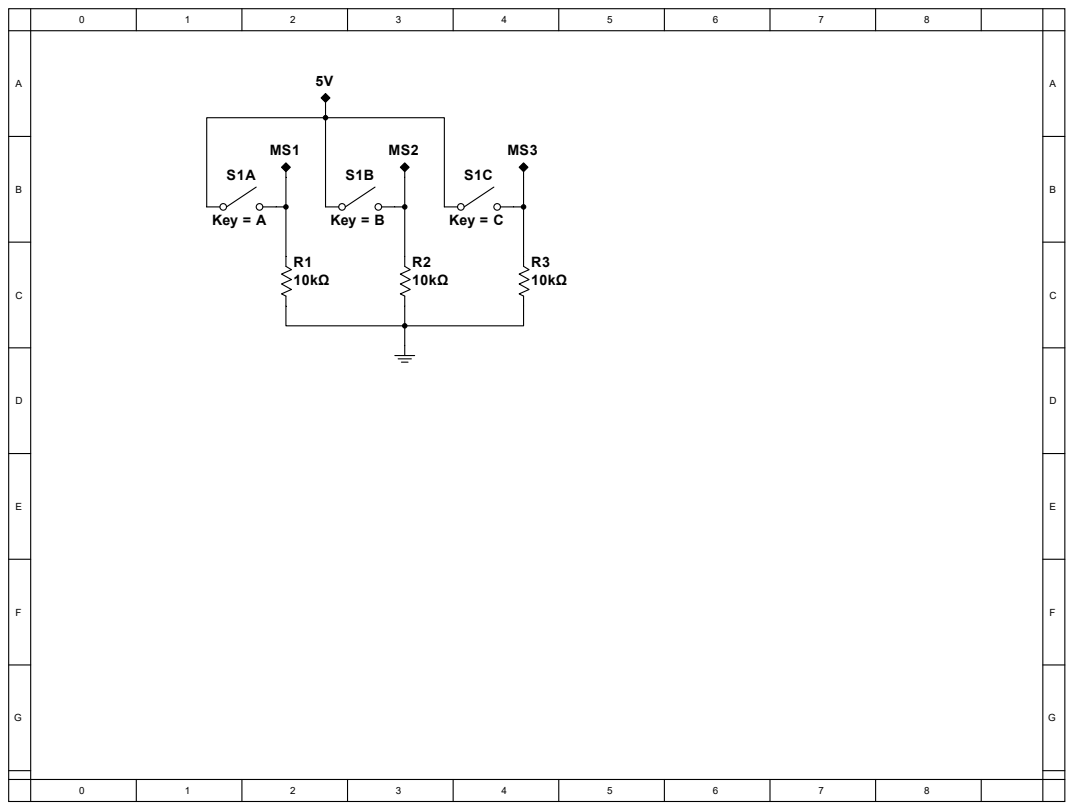
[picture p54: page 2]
Key = A; Key = B; Key = C

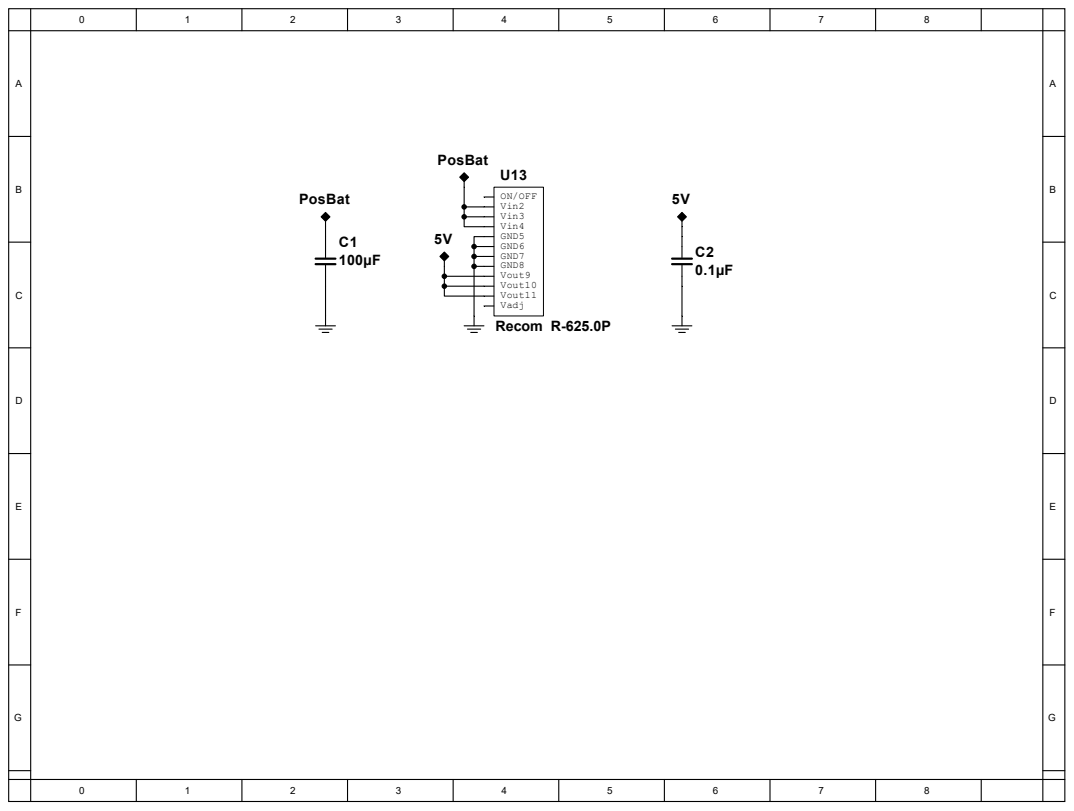
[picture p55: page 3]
PosBat; Recom R-625.0P; ON/OFF Vin2 Vin3 Vin4 GND5 GND6 GND7 GND8 Vout9 Vout10 Vout11 Vadj

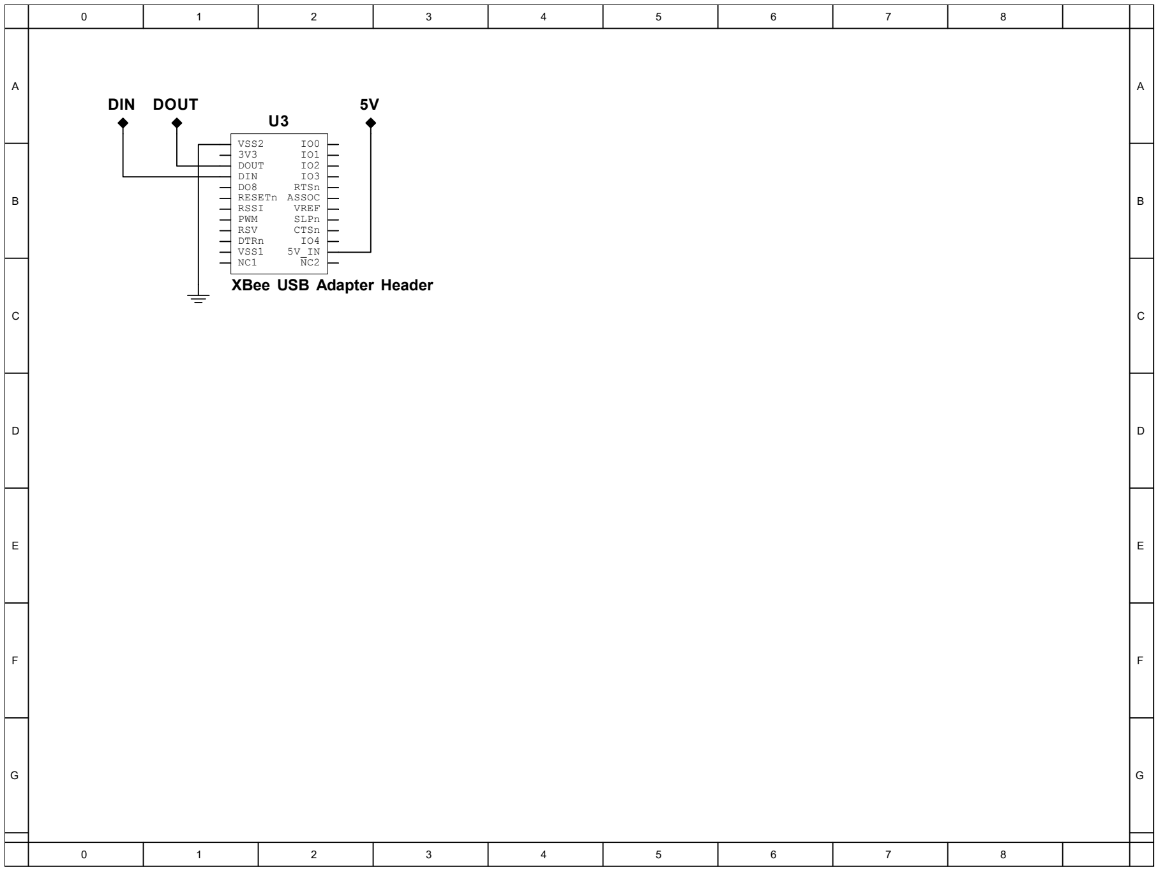
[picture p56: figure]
XBee USB Adapter Header; VSS2 3V3 DOUT DIN DO8 RESETn RSSI PWM RSV DTRn; VSS1; CTSn; SLPn; VREF; ASSOC; RTSn; DIN DOUT
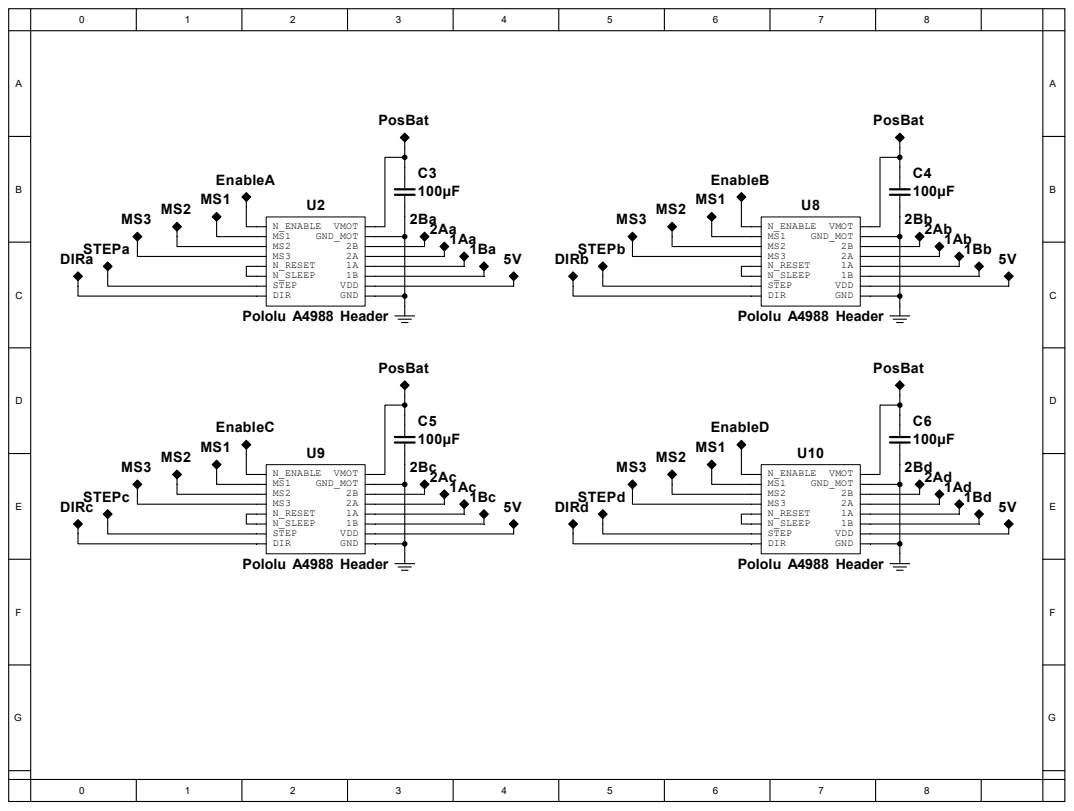
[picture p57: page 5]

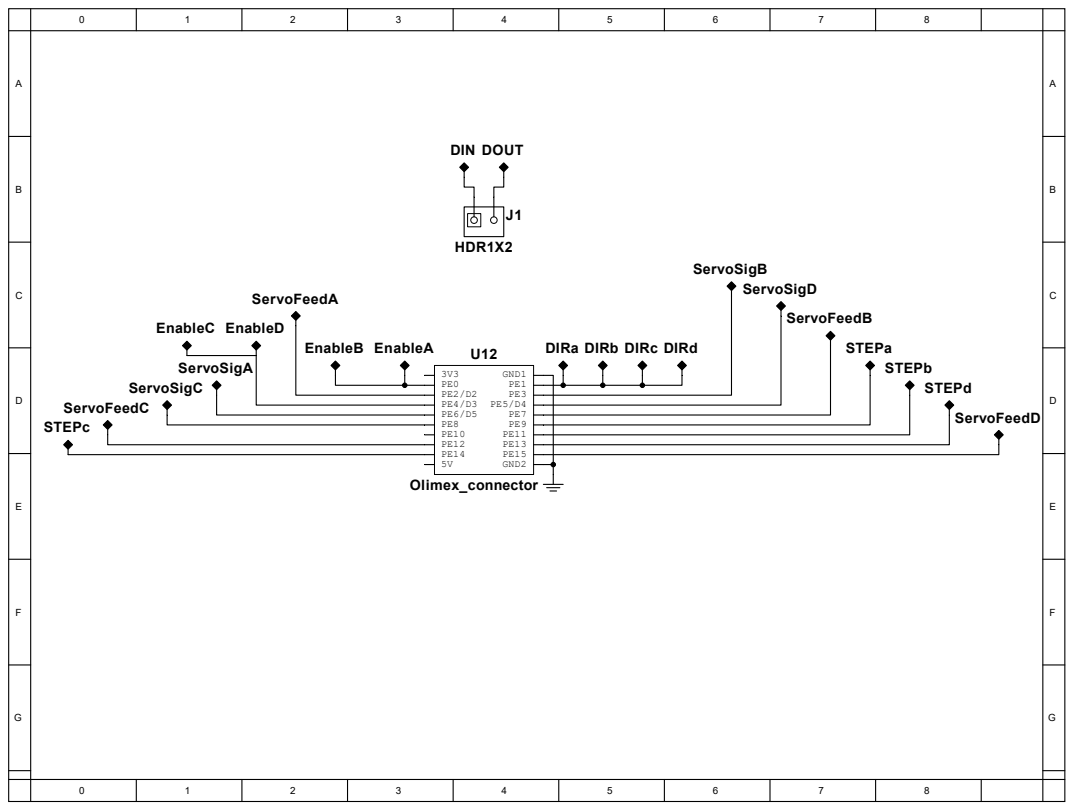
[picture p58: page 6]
Olimex_connector; GND2; GND1; EnableB EnableA; ServoSigA ServoSigC; STEPc; ServoSigB ServoSigD; STEPa STEPb STEPd; DIN DOUT; EnableC EnableD; ServoFeedA; ServoFeedB; ServoFeedC; ServoFeedD; HDR1X2

DIRa DIRb DIRc DIRd

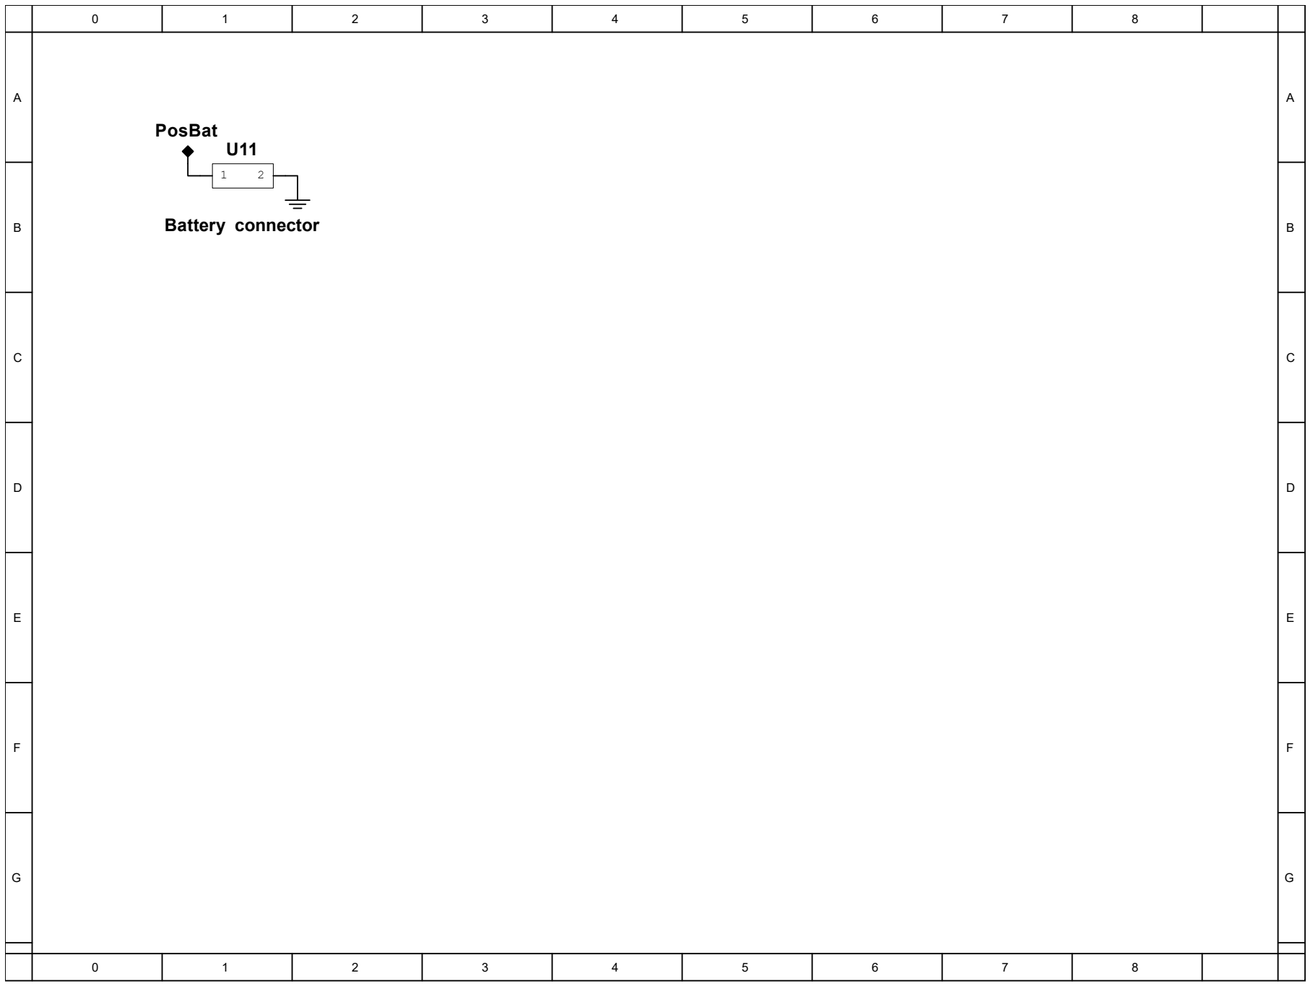
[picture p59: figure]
Battery connector; PosBat
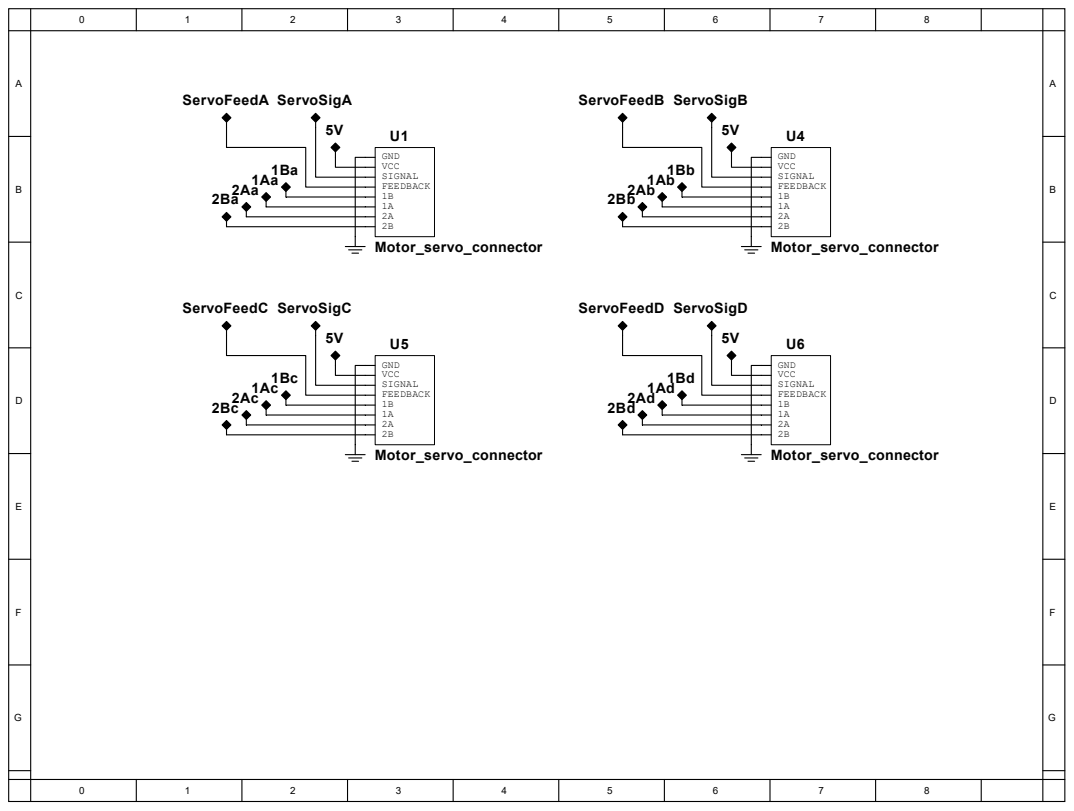
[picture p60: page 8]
ServoSigA; ServoSigB; ServoSigC; ServoSigD; ServoFeedA; ServoFeedB; ServoFeedC; ServoFeedD; Motor_servo_connector; GND VCC SIGNAL FEEDBACK 1B 1A 2A 2B

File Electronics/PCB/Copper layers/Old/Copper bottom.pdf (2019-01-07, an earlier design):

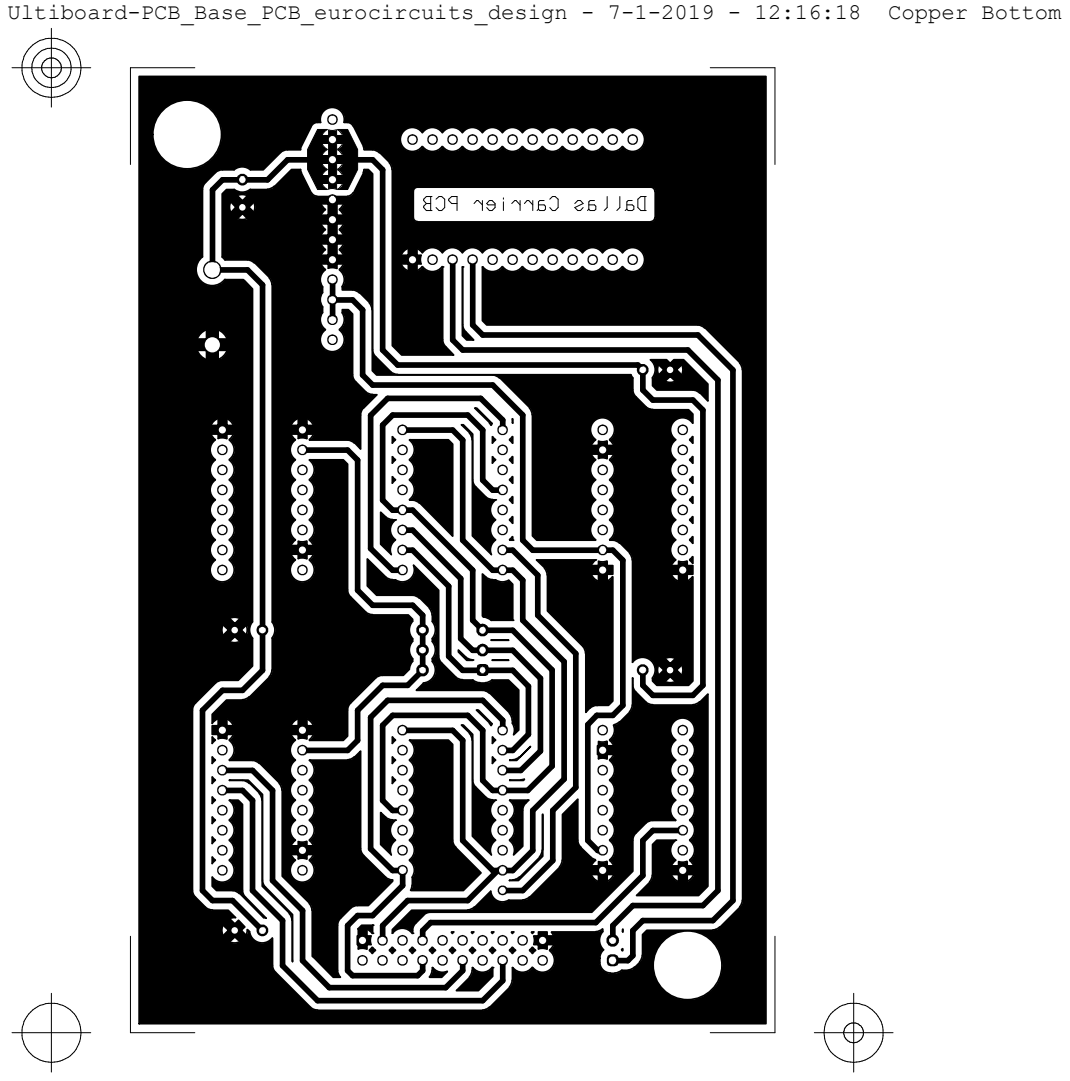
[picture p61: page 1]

Ultiboard-PCB_Base_PCB_eurocircuits_design - 7-1-2019 - 12:16:18 Copper Bottom

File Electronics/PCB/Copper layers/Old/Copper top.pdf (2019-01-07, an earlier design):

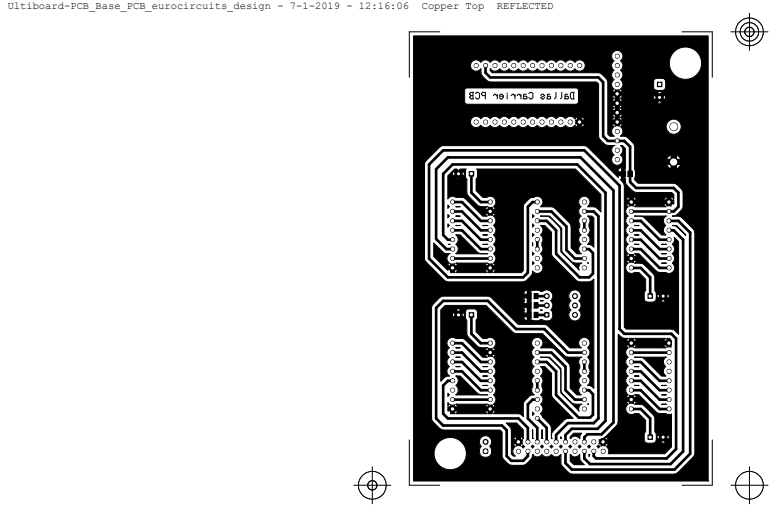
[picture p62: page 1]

Ultiboard-PCB_Base_PCB_eurocircuits_design - 7-1-2019 - 12:16:06 Copper Top REFLECTED

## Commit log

2018-11-12 Added dallas
    [Assembly Dolley chassis.SLDASM, Assembly Test chassis.SLDASM, Ball joint assy.SLDASM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]
2018-11-21 Added chassis drawing
    [Chassis.SLDPRT]
2018-11-26 Added drawings
    [Assembly Dolley chassis.SLDASM, Ball joint assy.SLDASM, Ball.SLDPRT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]
2018-11-27 Updated chassis
    [Dolly chassis test.SLDPRT]
2018-11-27 Combined the branches
    [Assembly_front.SLDASM, Bar.SLDPRT, Bar_connection_axle.SLDPRT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]
2018-11-28 Update Dolly chassis test.SLDPRT
    [Dolly chassis test.SLDPRT]
2018-11-28 Moved old files to another folder
    [Assembly_front.SLDASM, Bar.SLDPRT, Bar_connection_axle.SLDPRT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]
2018-11-28 Added new front
    [Foldable front base.SLDPRT, foldable front flap.SLDPRT, front assembly.SLDASM]
2018-11-28 Made side flaps
    [foldable front flap.SLDPRT, front assembly.SLDASM]
2018-11-30 Update Foldable front base.SLDPRT
    [Foldable front base.SLDPRT]
2018-11-30 Added side flap
    [Foldable front side flap.SLDPRT, foldable front flap.SLDPRT]
2018-11-30 Updated foldable front length
    [Foldable front base.SLDPRT, Foldable front side flap.SLDPRT, front assembly.SLDASM]
2018-11-30 Created left flap
    [Foldable front side flap left.SLDPRT]
2018-11-30 Made new chassis assembly
    [Assembly dolly.SLDASM]
2018-11-30 Update front assembly.SLDASM
    [front assembly.SLDASM]
2018-12-03 Added a folder for the fifth wheel
2018-12-03 made a fifth wheel
    [Fifth_wheel_disk.SLDPRT, Fifth_wheel_mount.SLDPRT]
2018-12-03 changed assembly
    [Assembly dolly.SLDASM, Dolly chassis test.SLDPRT]
2018-12-04 Adjusted the fifth wheel and added some extra parts to the fifth wheel
    [Fifth_wheel_assembly.SLDASM, Fifth_wheel_axle.SLDPRT, Fifth_wheel_disk.SLDPRT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]
2018-12-05 Cut chassis in half
    [Dolly chassis half 1.SLDPRT, Dolly chassis half 2.SLDPRT]
2018-12-05 Made new assembly
    [Chassis assembly 2.SLDASM]
2018-12-06 Copied existing parts of the front to adjust the width
    [Chassis assembly 2 - kopie.SLDASM, Foldable front base 2.SLDPRT, Foldable front side flap left 2.SLDPRT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]
2018-12-07 Updated chassis design
    [Chassis assembly 2.SLDASM, Dolly chassis half 1.SLDPRT, Dolly chassis half 2.SLDPRT]
2018-12-13 Added connection holes in chassis
    [Chassis assembly 2.SLDASM, Dolly chassis half 1.SLDPRT, Dolly chassis half 2.SLDPRT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]
2018-12-14 Update front assembly 2.SLDASM
    [front assembly 2.SLDASM]
2018-12-14 Added a folder for the PCB
2018-12-14 Added camera mount on front flap
    [Chassis assembly 2.SLDASM, foldable front flap 2.SLDPRT, front assembly 2.SLDASM]
2018-12-18 Combined chassis as one and created STL files
    [Assem1.SLDASM, Chassis assembly 2.SLDASM, Chassis assembly 3.SLDASM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]
2018-12-20 Made a schematic design and some components
2018-12-21 Made new front file for bleufox camera
    [Chassis assembly 3.SLDASM, Dolly chassis combined.SLDPRT, Dolly chassis combined.STL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]
2018-12-21 Moved components to new folder and adjusted the schematics
2018-12-21 Started pcb test design
2018-12-21 updated capacitor package
2018-12-21 Adjusted pin order motor_servo_connector
2018-12-21 Added PCB design files
2018-12-21 Made start with eurocircuits pcb design
2018-12-21 Made start with test PCB design
2019-01-03 finished the first version of the PCB design
2019-01-14 made a pdf of the schematics
2019-01-15 New chassis drawings and backup
    [Assem1.SLDASM, Assembly dolly.SLDASM, Assembly_front.SLDASM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]
2019-01-23 made some final adjustments and created the gerber files
    [PCB_Base_PCB_eurocircuits_design - Board Outline.gbr, PCB_Base_PCB_eurocircuits_design - Copper Bottom.gbr, PCB_Base_PCB_eurocircuits_design - Copper Top-Coppe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]
2019-01-24 Changed front flap to fit better on the base
    [Foldable front base 2.SLDPRT, foldable front flap 2.SLDPRT, front assembly 2.SLDASM]
